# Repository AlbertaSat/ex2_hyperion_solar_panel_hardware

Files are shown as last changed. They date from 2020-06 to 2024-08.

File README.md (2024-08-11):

# Hyperion_Solar_Panels

This repository contains documentation describing the design of modular, open-source, deployable panels for CubeSats. 

The directory of the repository contains:

	- Documentation
		- All documents describing the designs, methods to adapt the design, and methods to analyze the effectiveness of the design
  
	- PCB Design files
		- Altium Designer project files for AlbertaSat's open-source Solar Panel design, dubbed "Hyperion"
  
	- CAD Files
		- 3D CAD files of the panel designs and components used on the panels

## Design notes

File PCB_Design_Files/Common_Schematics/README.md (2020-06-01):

These are schematics used by all Hyperion Solar Panels.

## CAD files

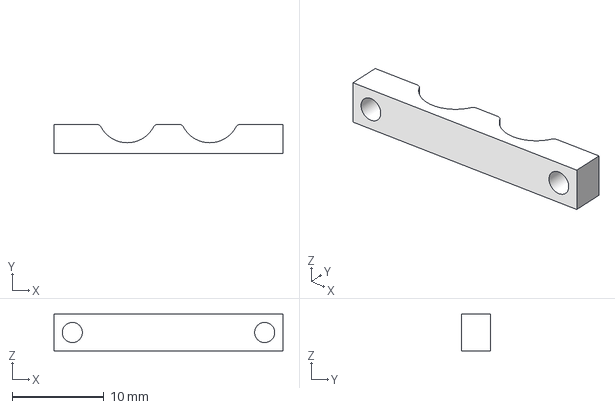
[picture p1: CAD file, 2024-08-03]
CAD_Files/20210528_DFGM_Saddle.step
25.0 x 3.18 x 4.00 mm

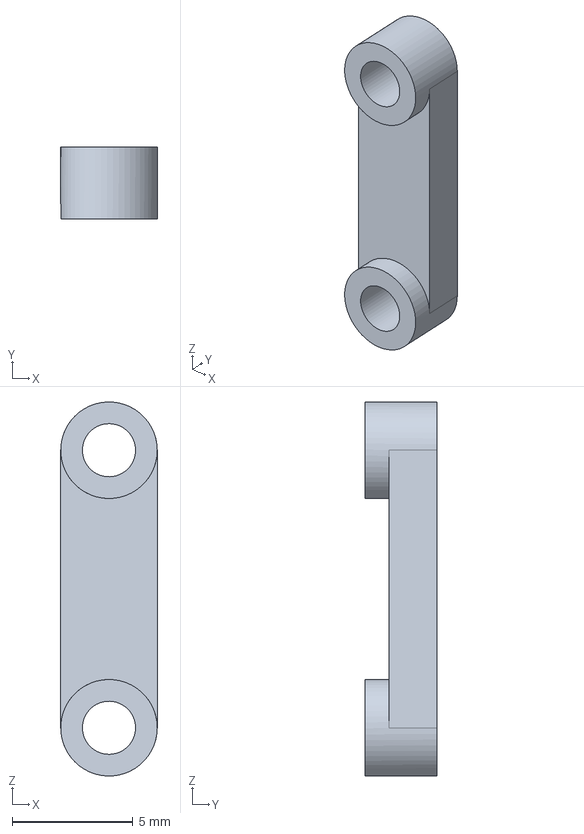
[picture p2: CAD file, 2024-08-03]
CAD_Files/20210528_Deployable_Switch_Depressor_Raised.step
4.00 x 3.00 x 15.5 mm

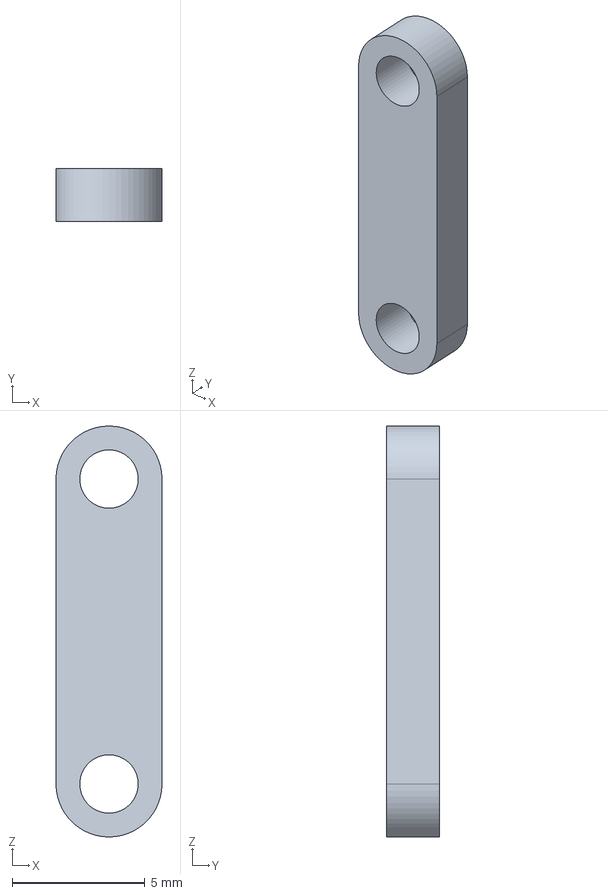
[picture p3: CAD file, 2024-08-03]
CAD_Files/20210528_Deployable_Switch_Depressor.step
4.00 x 2.00 x 15.5 mm

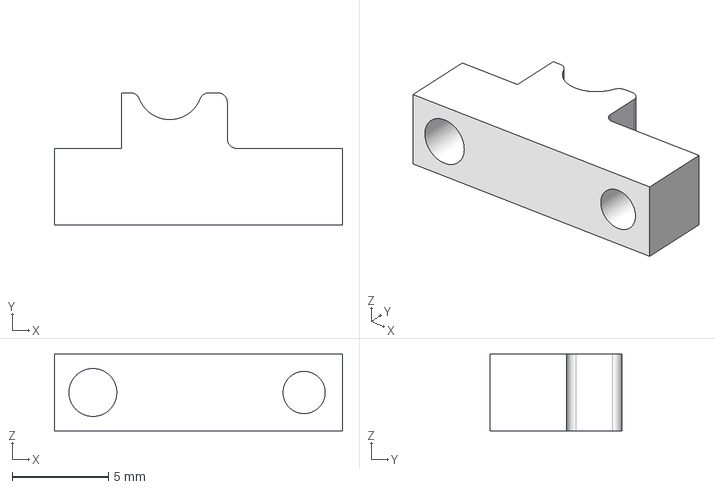
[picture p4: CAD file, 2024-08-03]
CAD_Files/20210823_Antenna_Saddle_2U.step
15.0 x 6.90 x 4.00 mm

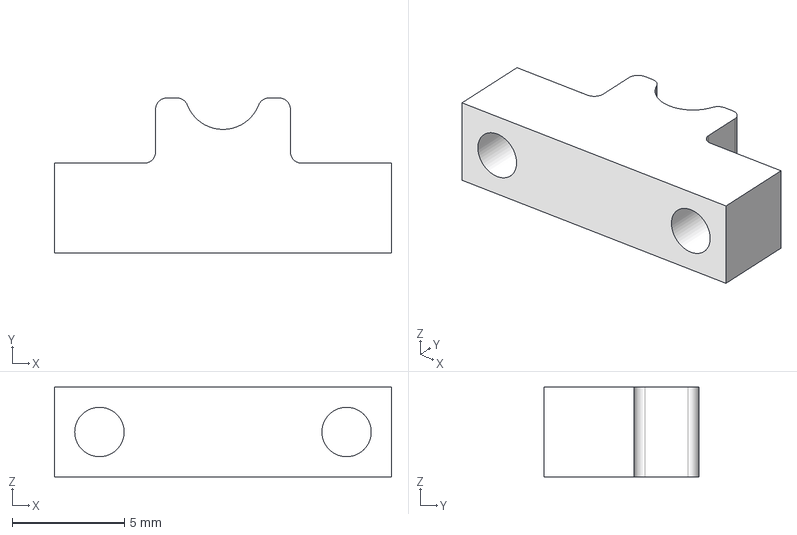
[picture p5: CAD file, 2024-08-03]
CAD_Files/20210528_Antenna_Saddle.step
15.0 x 6.90 x 4.00 mm

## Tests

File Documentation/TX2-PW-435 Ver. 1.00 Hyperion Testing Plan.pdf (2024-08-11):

# AlbertaSat

# Ex-Alta 2

# Hyperion Testing Plan

# Version 1.00

# July 20, 2020

University of Alberta

Institute for Space Science Exploration and Technology

Hyperion Testing Plan | TX2-PW-406 Ver. 1.00
AlbertaSat, University of Alberta | July 20, 2020

# Document Authentication

Prepared by

Name | Position | Signature | Date
Dineth Jayasekera | Power Team Member | | July 20, 2020
Nash Gould | Power Lead | | July 20, 2020

Reviewed by

Name | Position | Signature | Date
Nicholas J. Sorensen | Systems Engineer/Power Lead | | July 20, 2020
T. Haluza-Delay | Systems Engineer | | July 20, 2020

The undersigned acknowledge that they have reviewed the Hyperion Testing Plan, and they authorize the objectives, rules, and organization of the project as described in this document. Any changes to this Hyperion Testing plan will be coordinated with and approved by the undersigned or their designated representatives.

Approved by

Name | Position | Signature | Date
Nicholas J. Sorensen | Systems Engineer/Power Lead | | July 20, 2020
T. Haluza-Delay | Systems Engineer | | July 20, 2020

# Record of Document Changes

Version | Effective Date | Author(s) | Section(s) Changed | Description of Change(s)
0.10 | N/A | Dineth Jayasekera, Shirley Wang | All | Creation of Document
0.11 | July 10, 2020 | Nicholas J. Sorensen | All | Corrections in all sections, as well as formatting.
1.00 | July 20, 2020 | | All | PCB Component Testing Finalized

# Executive Summary

This document outlines the testing to be done on the various components of the Hyperion solar panel system being flown on the Ex-Alta 2 cubesat, and is largely based on standard ECSS-E-ST-20-08C [R1]. The following sections outline the equipment needed for tests, the safety measures taken before, during, and after testing, the procedures for each test, and the pass-fail criteria for each test.
The XTJ Prime solar cell assembly (SCA) will be tested to ensure that the cells meet the specifications outlined in the datasheet provided by Spectrolab, in addition to any other specifications given to AlbertaSat at the time of purchase. Testing done on the SCAs will include electrical performance testing, visual inspections, and verification of the pre-installed bypass diode on the XTJ-Prime solar cells. The solar panels, or the photo-voltaic assembly (PVA), will go through various qualification tests to ensure that they are capable of providing power required for the Ex-Alta 2 mission, in addition to withstanding a LEO environment. Testing on the PVA will include qualification testing and acceptance testing. This ensures that the Hyperion PVA is capable of performing as designed and will be ready for flight aboard Ex-Alta 2. Tests will ensure that the solar panels are capable of withstanding a range of temperatures and humidities, in addition to a reasonable amount of electro-static discharge (ESD). Testing on the Hyperion PVA will be conducted during and after assembly to ensure that the solar panels are built to mission specifications.

# Table of Contents

Document Authentication | 1
Record of Document Changes | 2
Executive Summary | 3
List of Figures | 8
Reference Documents | 9
Overview | 12
Safety and Handling Procedures | 13
Environmental Conditions | 13
Test tolerances and accuracies | 13
Parts, materials, and process parameters | 13
Toxicity | 13
Flammability | 14
Corrosion | 14
Magnetism | 15
Critical materials | 15
Solar cell assembly and component level testing | 16
Visual inspection | 16
Visual inspection for defects in the solar cell | 16
Visual inspection for defects In the coverglass | 17
Visual inspection for defects In the rear contacts | 18
Visual inspection for defects in the interconnectors | 18
Pass-fail criteria | 18
Dimensions and mass inspection | 18
Inspection of dimensions | 18
Mass compliance | 19
Electrical performance measurement | 20
PCB component testing | 22
Pre-PCB assembly testing | 22
Mechanical board dimension check | 22
Electrical continuity check | 22
Grounding resistance check | 23
Post-PCB assembly testing | 23
Electrical continuity check | 23

Magnetorquer testing | 24
Power Consumption | 24
Voltage Applications | 24
Photodiode testing | 25
Temperature sensor testing | 25
Voltage and current sensor testing | 26
Deployment mechanism testing | 29
Burnwire resistor cycling | 29
Burnwire thread burning | 29
Photovoltaic assembly testing | 30
SCA application testing | 30
Mass measurement | 30
Dry insulation test | 31
Adherence to PCB | 32
Visual Inspection | 33
Electrical continuity check | 34
Grounding resistance check | 36
Blocking diode Test | 36
Qualification testing | 37
Acceptance testing | 38
Definitions of tests | 39
Full visual inspection | 39
Electrical health check | 39
Electrical performance measurement | 39
Capacitance test | 39
Humidity Test | 42
Vacuum Thermal Cycling Test | 44
Acronyms and Abbreviations | 45
Appendix A: Hyperion Testing Parameters | 46
Appendix B: Equipment Calibration | 48
Vernier Caliper Padding | 48
Appendix C: Unnecessary Tests | 50
Electron Irradiation | 50
Photon Irradiation and Temperature Annealing | 51
Ultraviolet Exposure Test (UV) | 52
Thermo-Optical Data | 53
Coating Adherence | 55

Contact Thickness and Uniformity | 55
Temperature Coefficients Check | 56
Outgassing | 56
Surface Conductivity Test | 59
Reflectance Test | 59
Hemispherical Reflectance | 60
Coverglass gain-loss | 60
Active Passive Interface Test | 60
Spectral Response | 60
ESD Test | 60

# List of Figures

Table 1.1 - Temperature test tolerances
Figure 1.1 - WHMIS 2019 health hazard symbols
Figure 1.2 - WHMIS 2019 flammable/explosive hazard symbols Figure 1.3 - WHMIS 2019 corrosive hazard symbol
Figure 2.1 - Diagram of Cell Defects
Table 2.1 - Maximum Dimension of Each Defect
Figure 2.2 - Location of contacts
Figure 2.3 - Diagram of XTJ Prime Cell showing measurement points for cell thickness Figure 2.4 - I-V Measurement circuit schematic
Figure 2.5 - Electrical performance measurement set-up
Figure 2.6 - Characteristic I-V curve
Figure 3.1 - Voltage sense schematic
Figure 3.2 - Current sense schematic
Figure 3.3 - Burnwire resistor schematic
Figure 4.1 - Dry Insulation Test connections
Figure 4.2 - Attaching the 2 Kapton foils described in step 3 Figure 4.3 - Solar Cell Continuity Check Schematic
Figure 4.4 - Solar Panel Photodiode Sun Sensor Schematic
Figure 4.5 - Blocking Diode test schematic for the Port Solar Panel
Table 4.1 - The order of checks and tests to be done for each test
Table 4.2 - Shows the order in which checks should be run for acceptance testing. Figure 4.6 - Equivalent schematic of measurement circuit
Figure 4.7 - Physical Diagram of the Measurement Circuit
Figure 4.8 - a) A typical v-t characteristic (left)
and b) a realistic v-t characteristic due to parasitic inductance (right) Figure 4.9 - v-t characteristic with line of best fit
Figure 4.10 - A v-t characteristic with capacitance measurements
Fig 4.11 - PVA placed upright inside a Temperature - Humidity chamber

# Reference Documents

Ref. No | Document Name | Description
R01 | ECSS-E-ST-20-08C_REV-1-Photovoltaic Assemblies and Applications (https://drive.google.com/open?id=1e7iEEMibtRSNh4r5PsDM7qt9K71p06-v) | Standards document for PVA and SCA assembly.
R02 | XTJ Prime Solar Cell Datasheet (https://drive.google.com/file/d/0B97d2bqnH0zkVlVuVkE2MGp6ZE9UczJwQ3VCZWdjbzFfLW1r/view?usp=sharing) | XTJ Prime Solar Cell Datasheet.
R03 | 26.62 cm XTJ Prime Data Sheet (https://drive.google.com/open?id=183z8vA6ApDNlvgNMVB-VMi8t07TAn0pB)
R04 | Nimals Thesis - Nanosatellite Electrical Power System Development (https://drive.google.com/file/d/1hn5aqBO2z6VRZzP0JX6DqySkAxhxV4oR/view?usp=sharing)
R05 | Solar Panel GitHub Repository (https://github.com/AlbertaSat/Hyperion_Solar_Panels/)
R06 | ASTM E1462-12 Standard Test Methods for Insulation Integrity and Ground Path Continuity of Photovoltaic Modules | Used section 7.2 in page 3 for the Insulation Integrity, Insulation Resistance
R07 | Solar Cell Capacitance Determination Based on RLC Resonant Circuit | Used information from this to write the overview of a Capacitance Test in section 3.4.4
R08 | Solar Cell Capacitance Measurement Paper R. Blok (https://drive.google.com/file/d/14LIBwxDeGmqE0Z6AtOoJMlMoXcoapYHf/view?usp=sharing) | Research paper on Time domain capacitance measurement for Multi-Junction PVA and SCA
R09 | ASTM D1193-99: Standard Specification for Reagent Water | Standard Specification for Reagent Water
R10 | TX2-PW-406 Ver 1.00 Hyperion Solar Panels Interface Control Document (https://docs.google.com/document/d/1ZF8Y04XHxNmc1AYKCmSLeX3bC2qYf7z2ltytlE_TRUk/edit?usp=sharing)
R11 | CV-2289 Adhesive Datasheet (https://drive.google.com/file/d/1lksphBZLpFXucOKJV0rzpvgfndgTXVmK/view?usp=sharing)
R04 | Electrostatic Discharge Testing on Meteosat 3rd (https://drive.google.com/file/d/14aZHrpDwEIz-mOJ8zAYnhdjg1PYSGra5/view?usp=sharing)

| Generation Photovoltaic Assembly (https://drive.google.com/file/d/14aZHrpDwEIz-mOJ8zAYnhdjg1PYSGra5/view?usp=sharing)
R13 | ECSS-Q-ST-70-06C Particle and UV Radiation Testing for Space Materials (https://drive.google.com/file/d/1VEsK8YueqFWnclV3nJhuqDO76dNOLiTn/view?usp=sharing) | ECSS document detailing UV radiation process
R14 | Solar Cell Radiation Handbook NASA (https://drive.google.com/file/d/1d_dKATuudc_2SWbYDcYr1uuwGrd_dQxY/view?usp=sharing)
R15 | Thermal Annealing of Radiation Damage in Solar Cells - Goddard Space Flight Center (https://drive.google.com/file/d/1DUtyBk_aHcihWG-Gnc6Qpf9xUuCX0HYQ/view?usp=sharing)
R16 | Test Techniques for Voltage and Humidity-Induced Degradation of Thin Film Photovoltaic Modules -Jet Propulsion Laboratory (https://drive.google.com/file/d/1DUtyBk_aHcihWG-Gnc6Qpf9xUuCX0HYQ/view?usp=sharing)
R17 | ISO-23038: Space systems — Space solar cells — Electron and proton irradiation test methods | Electron and proton irradiation test methods for photovoltaic cells
R18 | ISO 9211-4: Optics and photonics - Optical coatings - Part 4 Specific test methods
R19 | Accelerated UV Testing and Characterization of PV Modules with UV - cut and UV - pass EVA Encapsulants by Kshitiz Dolia (https://drive.google.com/file/d/1_bruaEFhISPj-MZBzRWybPWMlPLE752r/view?usp=sharing)
R20 | Electrical Isolation Design and Electrochemical Corrosion in Thin Film Photovoltaic Modules -Jet Propulsion Laboratory (https://drive.google.com/file/d/1xiNpXD-C_T9-3XhJVlm7x-XevL9Cx3Tr/view?usp=sharing)
R21 | Solar Radiation - Qiang Fu, (https://drive.google.com/file/d/1PRftebfSfHzLcuw8mMy50l51dxaLHDcr/view?usp=sharing) Page 1859 | Got values of solar intensity of UV light from this (for the UV test)
R22 | ASTM E948-16: Standard Test Method for Electrical Performance of Photovoltaic Cells Using Reference Cells Under Simulated Sunlight

R23 | ASTM E2236 - Standard Test Methods for Measurement of Electrical Performance and Spectral Response of Non Concentrator Multijunction Photovoltaic Cells and Modules
R24 | ASTM: E1802 − 12 - Standard Test Methods for Wet Insulation Integrity Testing of Photovoltaic Modules
R25 | Solar Cell Performance Measurement F.C Treble (https://drive.google.com/file/d/1NRIMmkoJcFSVu136WJdcnpuidz_4xrMm/view?usp=sharing) | Research paper on basic methods of how solar cells can be measured (from 1965 so is a bit dated)
R26 | <Removed>
R27 | ecss-q-st-70-02c Thermal Vacuum Outgassing Test (https://drive.google.com/file/d/1gFmYXbCWnB96BwieAUklcGbwXe3g5Ucf/view?usp=sharing) | ECSS document detailing how the Thermal Vacuum Outgassing test should be carried out

# Overview

This document outlines the testing to be done on the various components of the Hyperion solar panel system being flown on the Ex-Alta 2 cubesat, and is largely based on standard ECSS-E-ST-20-08C [R01]. The following sections outline the equipment needed for tests, the safety measures taken before, during, and after testing, the procedures for each test, and the pass-fail criteria for each test.
The XTJ Prime solar cell assembly (SCA) will be tested to ensure that the cells meet the specifications outlined in the datasheet provided by Spectrolab, in addition to any other specifications given to AlbertaSat at the time of purchase. Testing done on the SCAs will include electrical performance testing, visual inspections, and verification of the pre-installed bypass diode on the XTJ-Prime solar cells. The solar panels, or the photo-voltaic assembly (PVA), will go through various qualification tests to ensure that they are capable of providing power required for the Ex-Alta 2 mission, in addition to withstanding a LEO environment. Testing on the PVA will include qualification testing and acceptance testing. This ensures that the Hyperion PVA is capable of performing as designed and will be ready for flight aboard Ex-Alta 2. Tests will ensure that the solar panels are capable of withstanding a range of temperatures and humidities, in addition to a reasonable amount of electro-static discharge (ESD). Testing on the Hyperion PVA will be conducted during and after assembly to ensure that the solar panels are built to mission specifications.
The tests in this document should be performed in the following order:
1. SCA Acceptance Tests (Chapter 2)
2. PCB Component Tests (Chapter 3)
3. PVA Tests (Chapter 4)
a. In-Process PVA Tests
b. Qualification PVA Tests
c. Acceptance PVA Tests
The solar panels will have been qualified engineering models once all SCA acceptance tests have been performed on the solar cells, the PCB component tests have been performed on each panel, and the PVA tests have been performed on each panel.

# 1. Safety and Handling Procedures

The following procedures are to be followed in all testing and handling of Hyperion components to ensure operational safety.

## 1.1. Environmental Conditions

Atmospheric conditions during inspection, testing, and storage, unless specified otherwise, must be as follows:
1. Pressure: 101.325 ± 3.3 kPa
2. Temperature: 23 ± 5 C
3. Average relative humidity: 40 - 60%
In addition, the room cleanliness level should be airborne particle count: Class 8 ISO 14644-1. Any deviation from the above conditions should be recorded [R1].

## 1.2. Test tolerances and accuracies

In the following tests, the accuracy of the instruments and equipment used to measure and control test parameters should be an order of magnitude higher than the tolerance on the variable to be measured, with the exception of mass and temperature measurements. The accuracy of mass measurements should be better than ±1% of the mass or 0.01g, whichever is more accurate. The test temperature tolerances for any thermal testing are given in table 1.1 below. All equipment and instruments used should be calibrated properly before testing. Instruments should be recalibrated daily during testing [R01].
Vernier Calipers should always be padded before use in measurement. Refer to 5.3 Vernier Caliper Padding
Temperature Range (°C) | Tolerance (°C)
-40 to -30 | -10/0
-30 to +60 | -5/+5
+60 to +70 | 0/+10

Table 1.1 - Temperature test tolerances. This shows the maximum acceptable deviation in temperature during a thermal test [1] i.e. the temperature can vary from -50 to -40 when conducting thermal cycling at -40 ℃.

## 1.3. Parts, materials, and process parameters

### 1.3.1. Toxicity

1. Identify, and create a log of materials used during the design/construction process that can cause injury. Toxic materials can be identified by checking the case/packaging for the below Hazard symbols

Figure 1.1 - WHMIS 2019 health hazard symbols

2. Not all companies use these symbols so also look for health/toxicity warnings on labels
3. Use gloves and other appropriate protective apparel when handling toxic materials (ie: face masks)
4. Describe precautions to be taken when handling these materials.

### 1.3.2. Flammability

1. Identify, and create a log of flammable materials used in the design/construction process. Toxic materials can be identified by checking the case/packaging for the below Hazard symbols

Figure 1.2 - WHMIS 2019 flammable/explosive hazard symbols

2. Not all companies use these symbols so look for warnings about flammability/ combustibility on labels.
3. Ensure that flammable materials are stored safely, and are not used in situations where they may combust (ie: used near possible ignition sources and oxygen)

### 1.3.3. Corrosion

1. Consider the effects of corrosion on the photovoltaic cells during both storage, and during operation. This can be done by estimating the corrosion rate of the PVA system for both the duration in storage and in operations and estimating the level to which the PVA might corrode in that duration.
2. Take the atmosphere conditions 101.325 kPa at 27 C for 5 years.

Figure 1.3 - WHMIS 2019 corrosive hazard symbol

3. Look for electrolytic corrosion erosion near metal-metal interfaces with current flow, and contact with an electrolyte. This is most common near batteries or similar devices.

### 1.3.4. Magnetism

1. Use only non-magnetic materials. Any permanent magnets used should be recorded. Check for closed loops in the PCB, 90° angle traces, and minimum high speed trace lengths by reviewing all board designs for Hyperion. The Hyperion does not have high speed traces however this is something to keep on mind.

### 1.3.5. Critical materials

1. All silver cladding used must be annealed, and must be 99.9% pure silver
2. There can be no pure Tin, Cadmium, or Zinc in the finished space-qualified solar panels.
a. Pure Tin can be a tin alloy with less than three atomic percent of the alloying metal.
b. Pure Cadmium and Zinc refer to when they are used non-mixed or unalloyed.
3. Solar panels containing Beryllium Oxide should be clearly identified
All of these requirements are from [R01].

# 2. Solar cell assembly and component level testing

Testing done on the SCA will be to verify that the XTJ Prime solar cells will perform to specification given in the datasheet in [R02]. All testing in this section is to be done at atmospheric pressure and room temperature. Testing on XTJ Prime solar cells will involve visual inspections, power generation characterisation, and bypass diode characterisation.

## 2.1. Visual inspection

All SCAs received from Spectrolab must be visually inspected to ensure that they are free of physical defects and that they are within the dimensions given within the datasheet. The following tests analyze the various parts of the SCA and ensure that each is capable of performing properly and withstanding a LEO environment [R01].

Materials:
1. Magnifying glass
2. Padded Digital vernier calipers - Refer to Vernier Caliper Padding

### 2.1.1. Visual inspection for defects in the solar cell

1. Search for edge chips, corner chips, surface nicks and record any found.
a. Edge chips: Defects along the edges of the cell
b. Corner Chips Defects near the corners of the cell
c. Surface nicks: Defects or blemishes on the surface of the cell
2. Estimate the length, and area of each defect using calipers and your judgement. The maximum length of each defect is shown below. Solar cells which fail this criteria will be rejected.

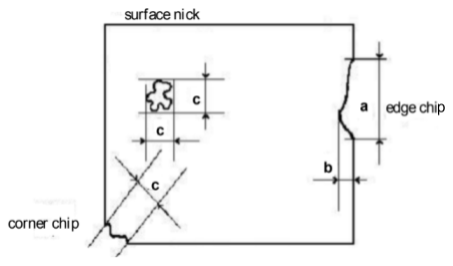
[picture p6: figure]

Figure 2.1 - Diagram of Cell Defects [1]

a | b | c
12 | 1.1 | 5

Table 2.1 - Maximum Dimension of Each Defect (mm) [R01]

3. The sum of all the areas of the defects found in step 2 must not exceed 1.33 cm

2
4. Focus on defects in the contact weld area as these could weaken interconnections between cells. Use judgement to decide whether the defects will cause any problems.
5. Check for fingerprints. Clean any found using Isopropyl alcohol and cleanroom wipes. Clean by wiping in one direction, the perpendicular direction and repeating.

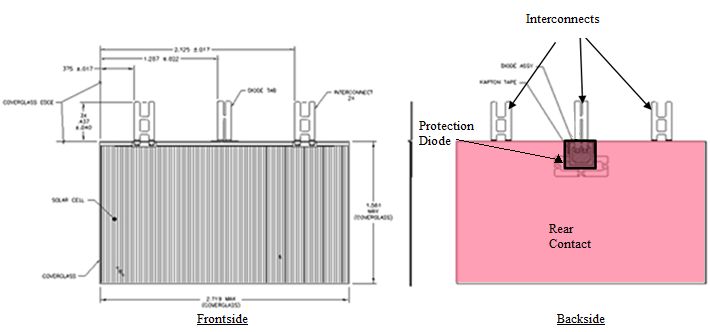
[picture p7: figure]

Figure 2.2 - Location of contacts

### 2.1.2. Visual inspection for defects In the coverglass

1. Inspect the SCA to ensure that the coverglass covers 100% of the bare solar cell.
2. Small surface defects less than 5mm in length on the coverglass can be ignored if the coverglass completely covers the solar cell.
3. Coverglasses with dirty and contaminated surfaces cannot be used. Clean using the isopropyl alcohol and cleanroom wipes. Carefully wipe in one direction, then wipe perpendicularly. Repeat.
4. Check for areas where the anti-reflective coating is missing/ scraped off. Estimate the area of any such regions. The sum of all such regions cannot exceed 0.8 cm

2
5. The coverglass should not contain any bubbles larger than 0.02mm

2
. Measure areas using
digital vernier calipers.
6. A coverglass cannot have
a. Cracks with a visible separation

b. More than 3 cracks
c. Meeting cracks with non-meeting ends separated by more than 2 mm
7. There should be no discolouration or delamination of the adhesive except in the area opposite the rear welds (where the connecting cells rear welds would attach)
8. Voids in the adhesive must be less than 0.6 mm in depth
9. The total estimated area of bubbles should not exceed 0.5 mm

2
- bubbles smaller than 0.02 mm

2
, and bubbles less than 2 mm away from the interconnector edges can be ignored for this test.

### 2.1.3. Visual inspection for defects In the rear contacts

1. Any SCAs with the following defects should not be used
a. Any drops and spatter are smaller than 0.1 mm in diameter and 0.05 mm in height.
b. Edge delaminations should not exceed 0.75 mm.
c. Defects should not exceed 5.3 mm

2

### 2.1.4. Visual inspection for defects in the interconnectors

There can be no breaking, tearing, or deformation of the interconnectors.

Pass-fail criteria
SCAs which do not meet the above requirements should not be used in the final PVA. These cells can be used for testing if the defect does not change the property being tested for.

## 2.2. Dimensions and mass inspection

### 2.2.1. Inspection of dimensions

This checks that the SCAs meet the dimensions given in the XTJ Prime documentation [R02].

Materials:
- Measuring tape
- Padded Digital vernier calipers/micrometer
- Mass scale
- Cleanroom wipes
- Isopropyl alcohol (99% or higher)

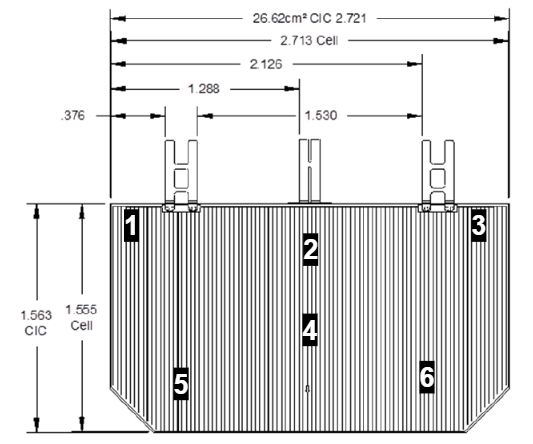
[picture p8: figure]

Figure 2.3 - Diagram of XTJ Prime Cell showing measurement points for cell thickness [R03]

Procedure:
1. Use the measuring tape to measure the length of each side of the SCA, and note down the dimensions of each SCA.
2. Measure and note down the thickness of the SCA at the numbered points shown in Figure 2.3 using calipers. Calculate the average thickness.
3. Check if the average thickness is between 80-225 µm. Note any cells which fall outside of this range.
4. Compare measured dimensions with the circuit diagrams, and footprints to ensure that all SCAs fit within the outlines of the PCB Board.

### 2.2.2. Mass compliance

Weigh each solar cell on a mass balance that meets the minimum tolerance stated in Section 1.2. Divide the mass of each Solar cell by its total area (Mass / 26 cm^2) and check if the obtained value is between 50-84 mg/cm^2 [R02]. Any solar cells outside of this range do not meet Mass Compliance.

## 2.3. Electrical performance measurement

This test measures the full IV characteristic curve of the XTJ Prime SCAs. Isc, Voc and Pmax are found/calculated from the curve. The measured Isc, Voc, and Pmax of the SCA are compared with the expected values.

Follow the manufacturer’s guidelines when setting up and calibrating the Solar Simulator.

Materials:
- Calibrated continuous solar simulator (Probably G2V Optics)
- Dark box/room
- Decade box
- Arduino system for data logging with current and voltage sensors

Procedure
1. Ensure that the solar simulator has been calibrated to emit 1 S.C (solar constant) at AM0, there is no spectral mismatch, and that the testing area is lit uniformly using test in appendix A.
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

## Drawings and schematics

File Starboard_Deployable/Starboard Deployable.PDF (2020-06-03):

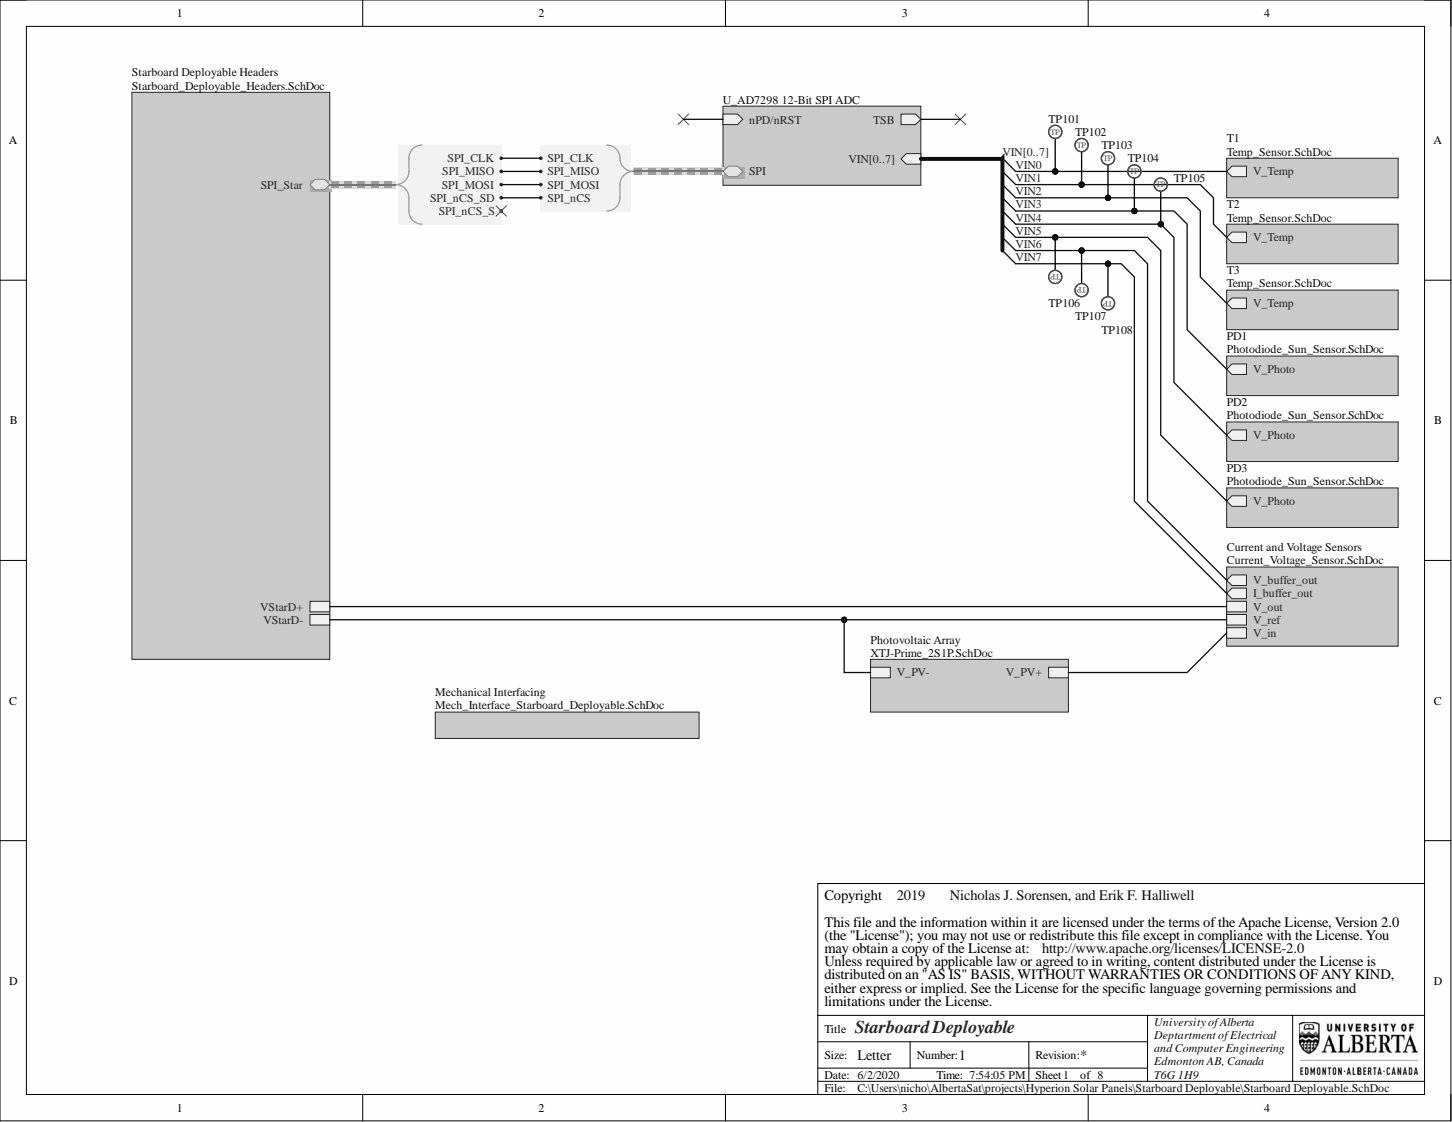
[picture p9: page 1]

(the "License"); you may not use or redistribute this file except in compliance with the License. You This file and the information within it are licensed under the terms of the Apache License, Version 2.0

may obtain a copy of the License at:
Unless required by applicable law or agreed to in writing, content distributed under the License is
distributed on an "AS IS" BASIS, WITHOUT WARRANTIES OR CONDITIONS OF ANY KIND, either express or implied. See the License for the specific language governing permissions and

http://www.apache.org/licenses/LICENSE-2.0

limitations under the License.
Starboard Deployable
Title

Letter
C:\Users\nicho\AlbertaSat\projects\Hyperion Solar Panels\Starboard Deployable\Starboard Deployable.SchDoc

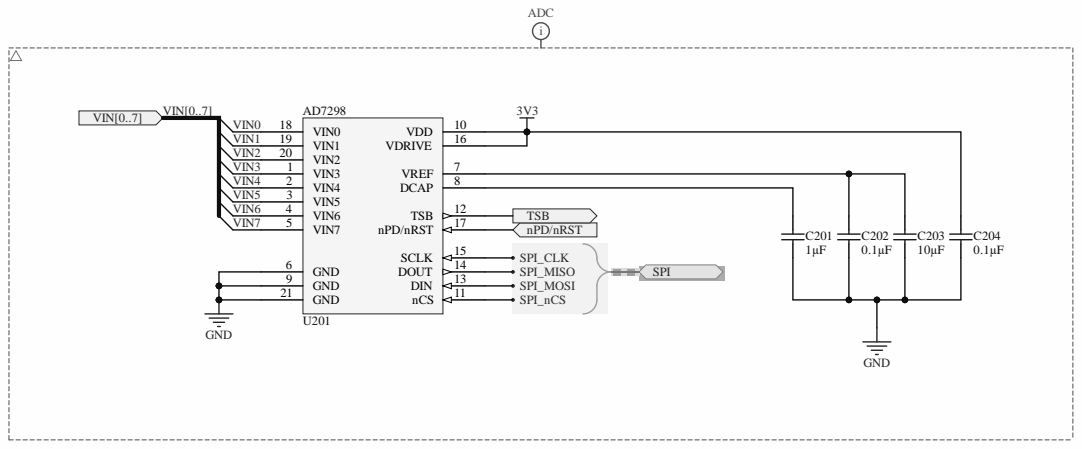
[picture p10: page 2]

1 2
1 7

9 | 1 3
2 1 | | 1 1

n within it are lic

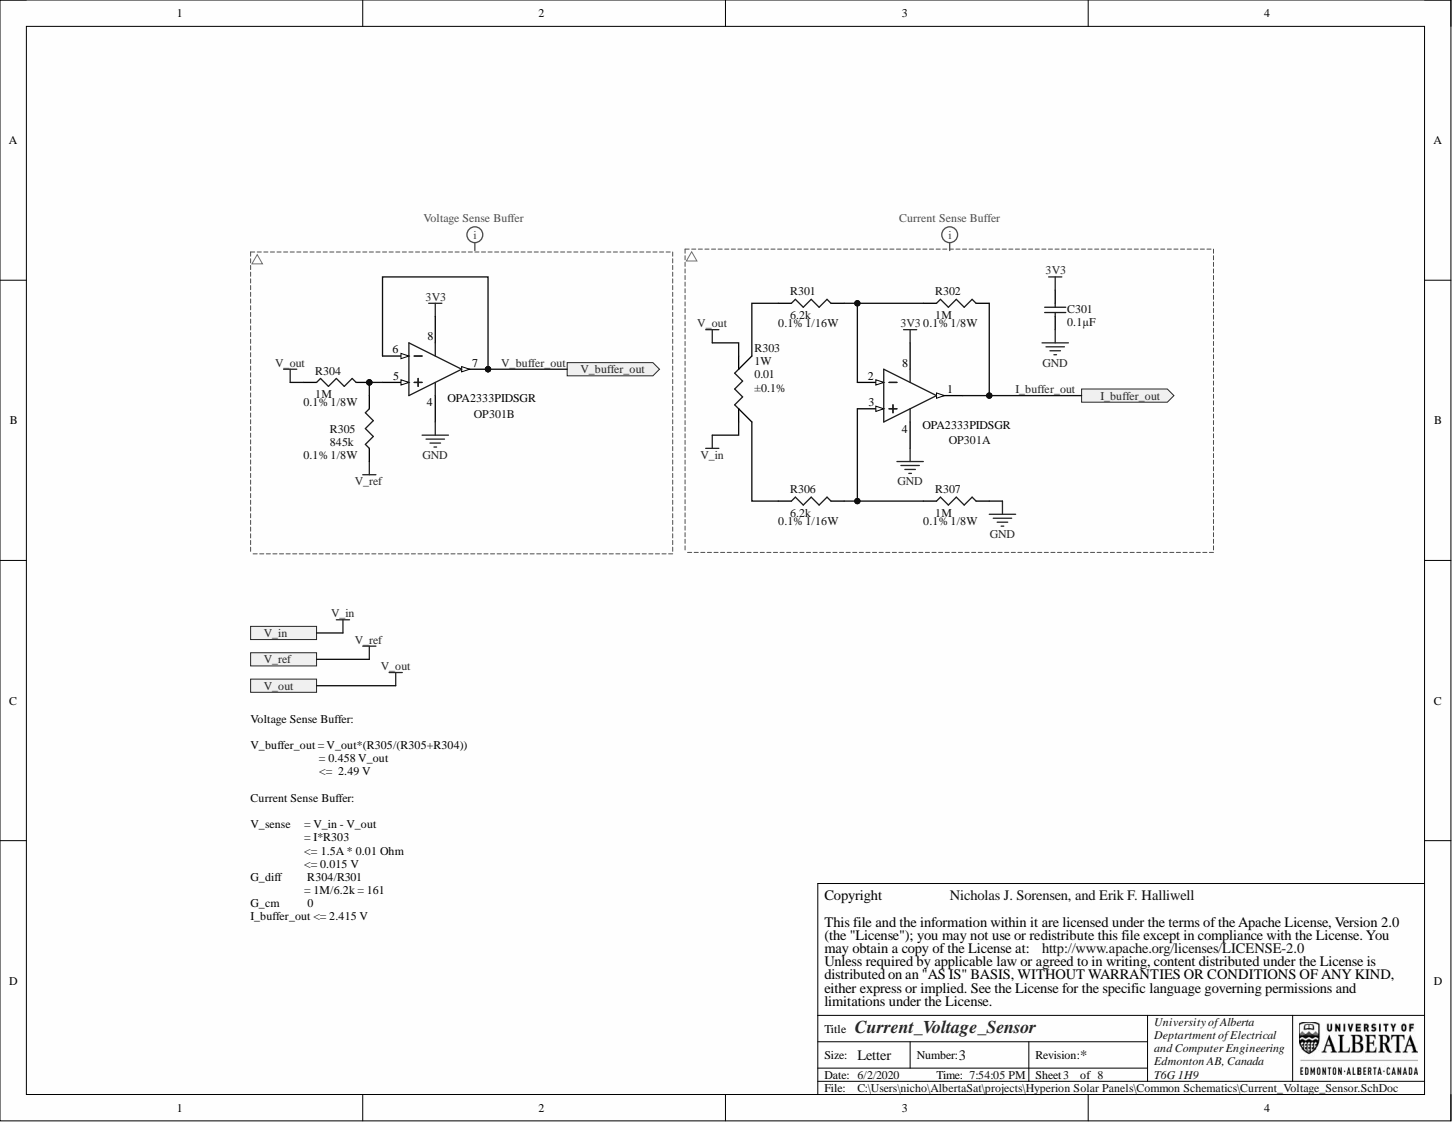
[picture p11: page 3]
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

http://www.apache.org/licenses/LICENSE-2.0

Letter
C:\Users\nicho\AlbertaSat\projects\Hyperion Solar Panels\Common Schematics\Current_Voltage_Sensor.SchDoc

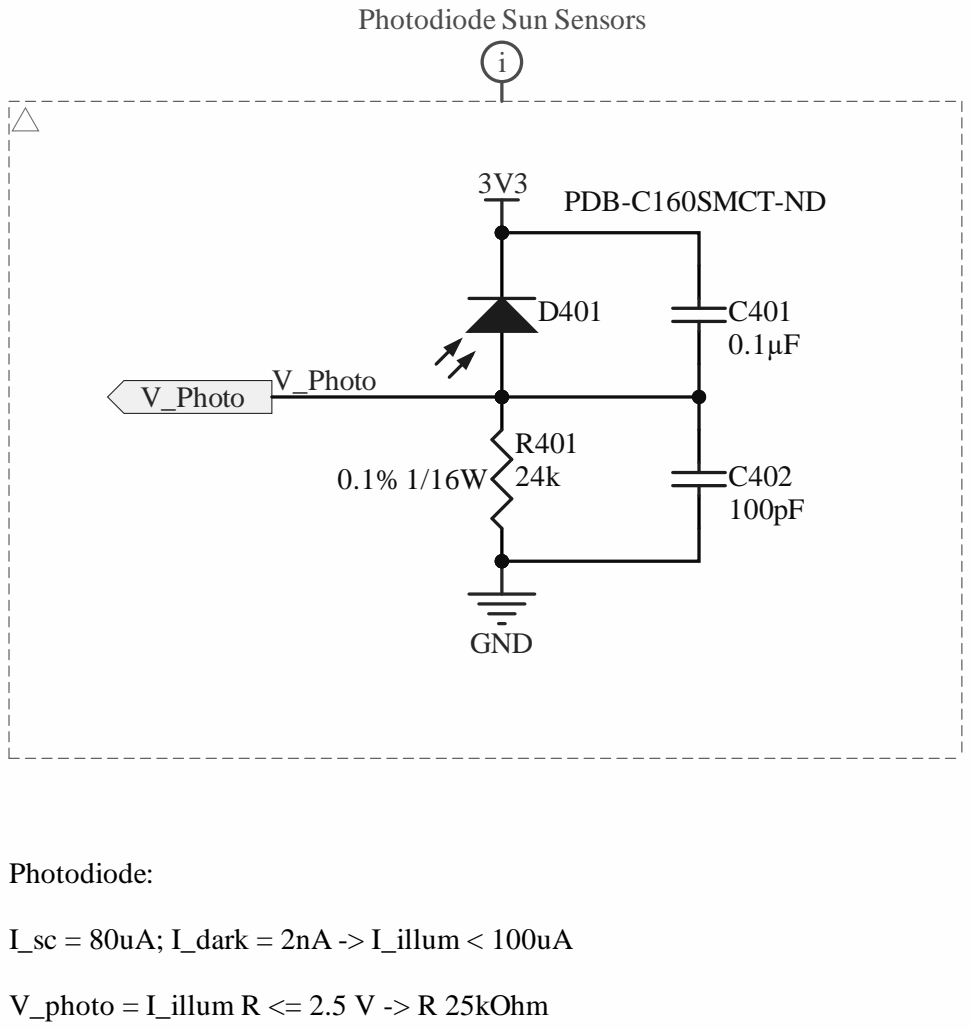
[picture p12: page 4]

n within it are lic

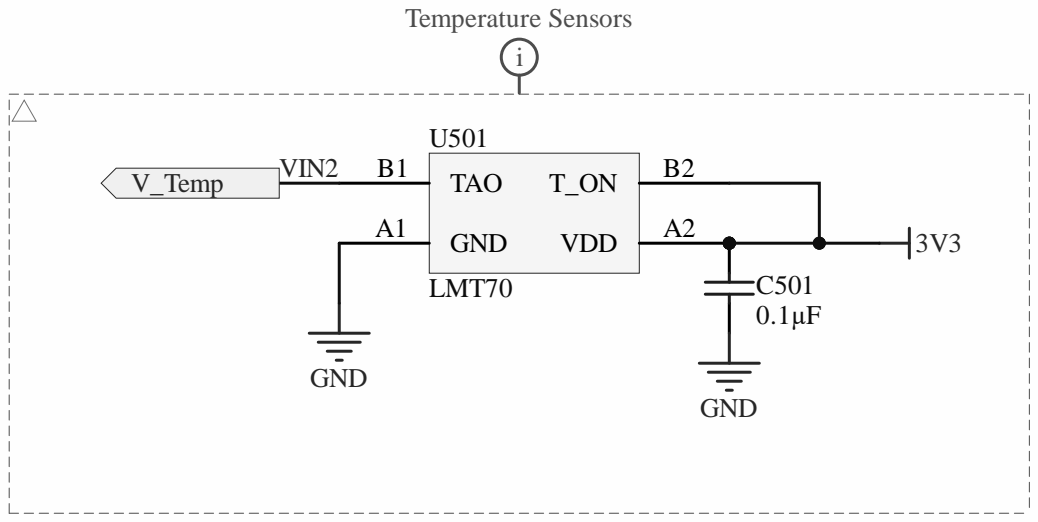
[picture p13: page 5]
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

http://www.apache.org/licenses/LICENSE-2.0

Letter
C:\Users\nicho\AlbertaSat\projects\Hyperion Solar Panels\Common Schematics\Temp_Sensor.SchDoc

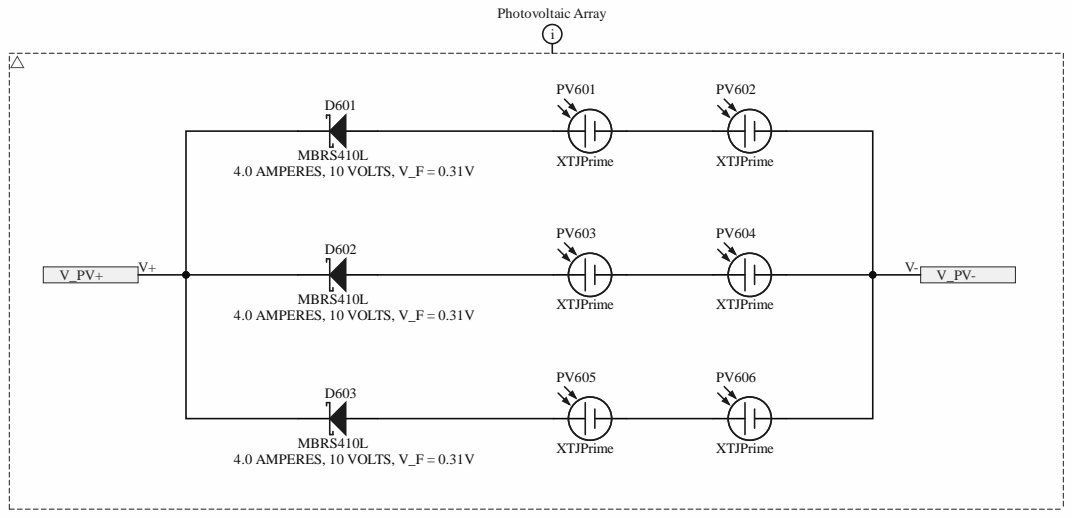
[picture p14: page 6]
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

http://www.apache.org/licenses/LICENSE-2.0

limitations under the License.
XTJ-Prime_2S2P
Title

Letter
C:\Users\nicho\AlbertaSat\projects\Hyperion Solar Panels\Common Schematics\XTJ-Prime_2S1P.SchDoc

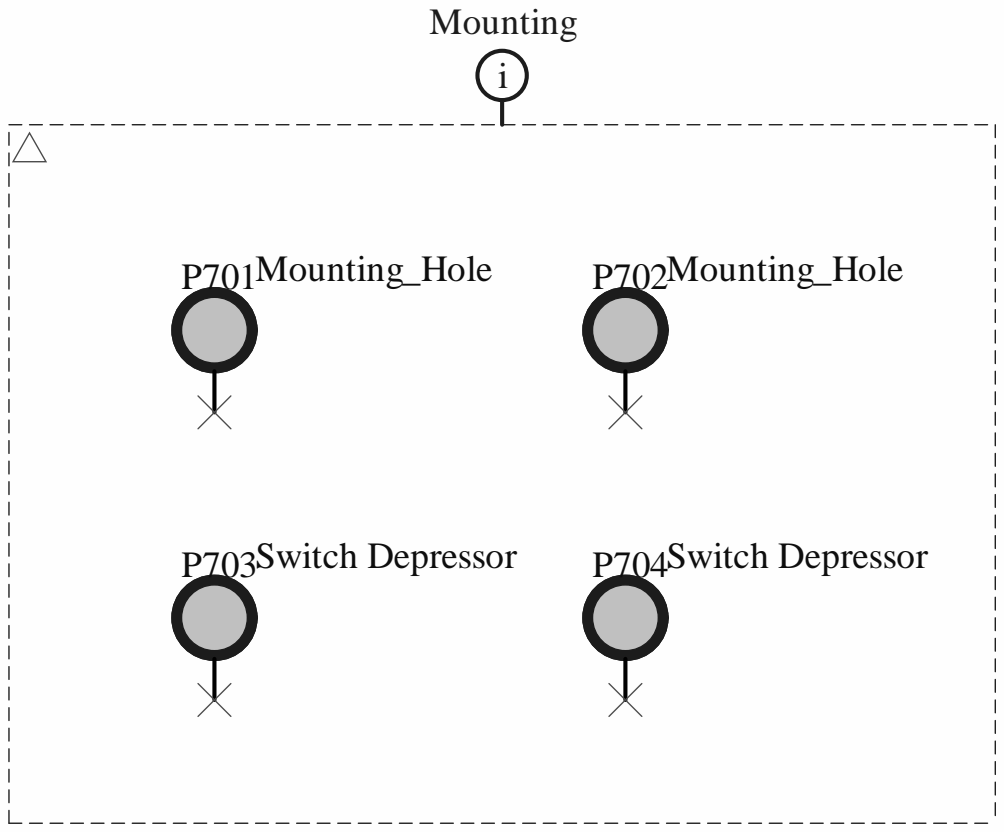
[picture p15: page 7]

n within it are lic

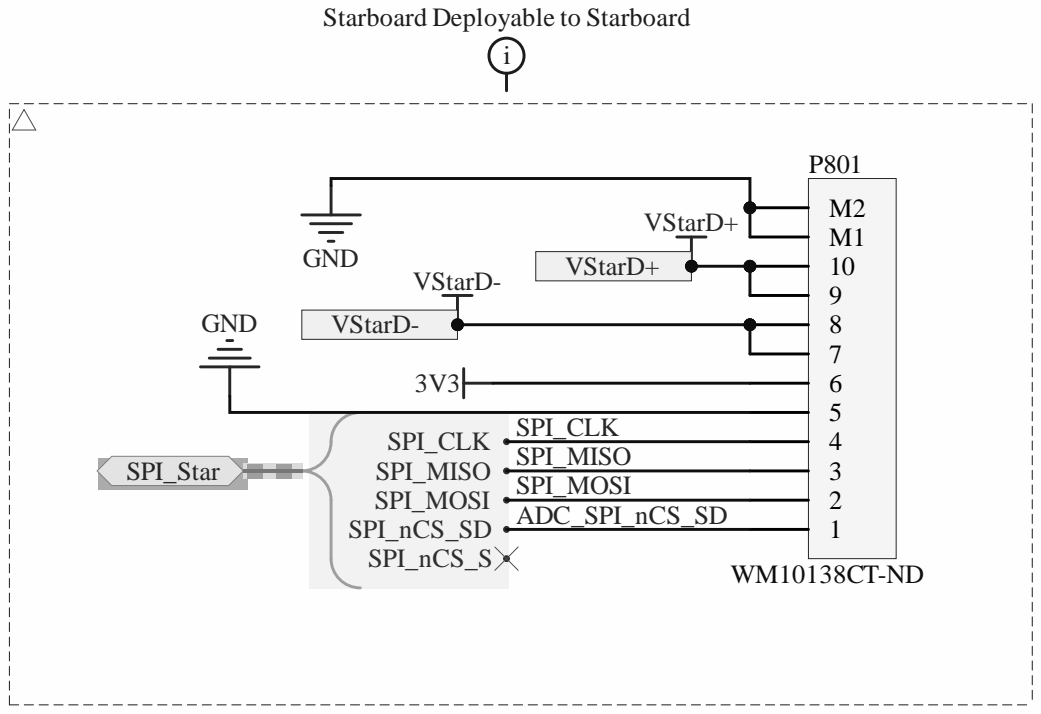
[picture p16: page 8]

Starboard Deployable to Starboard

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

http://www.apache.org/licenses/LICENSE-2.0

Letter
C:\Users\nicho\AlbertaSat\projects\Hyperion Solar Panels\Starboard Deployable\Starboard_Deployable_Headers.SchDoc

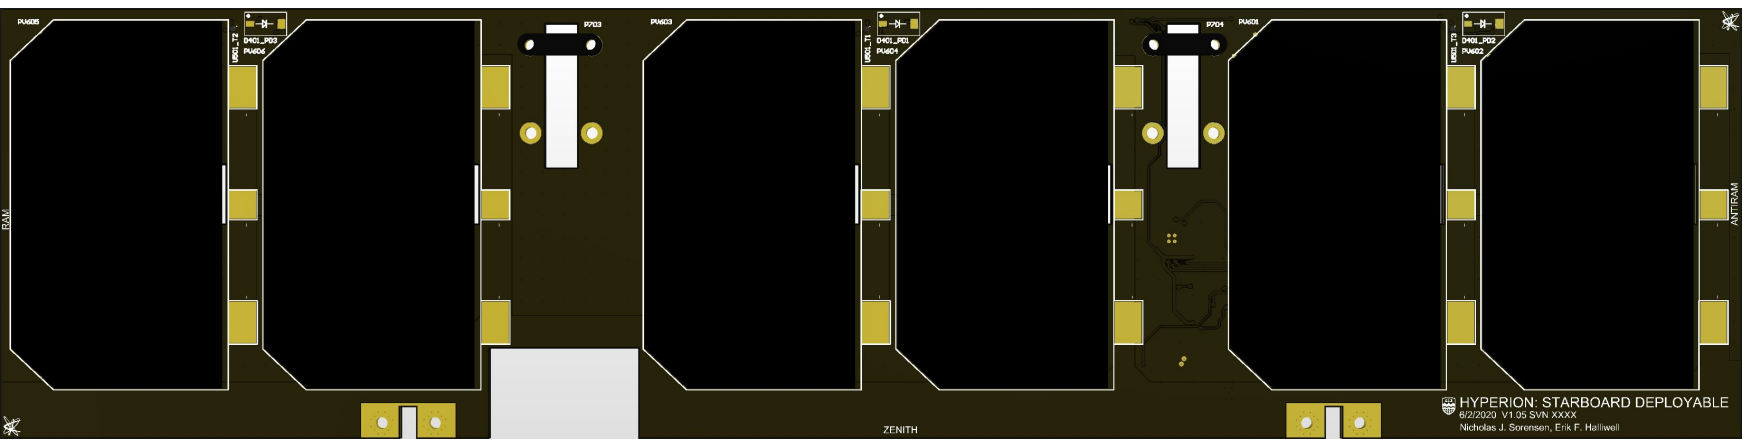
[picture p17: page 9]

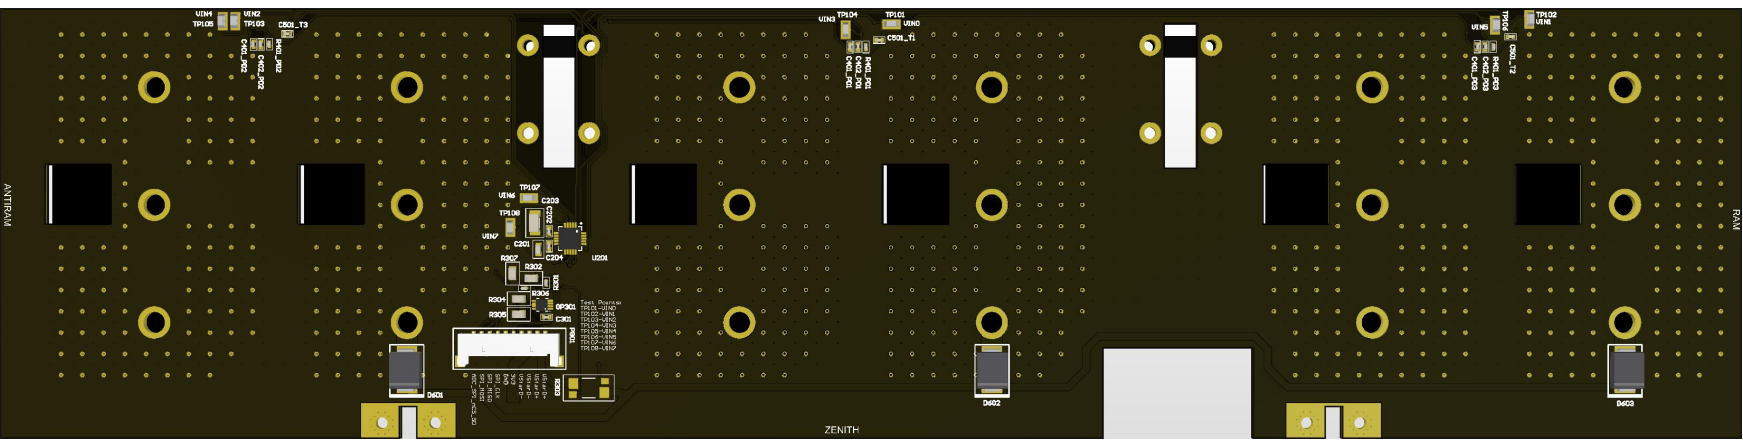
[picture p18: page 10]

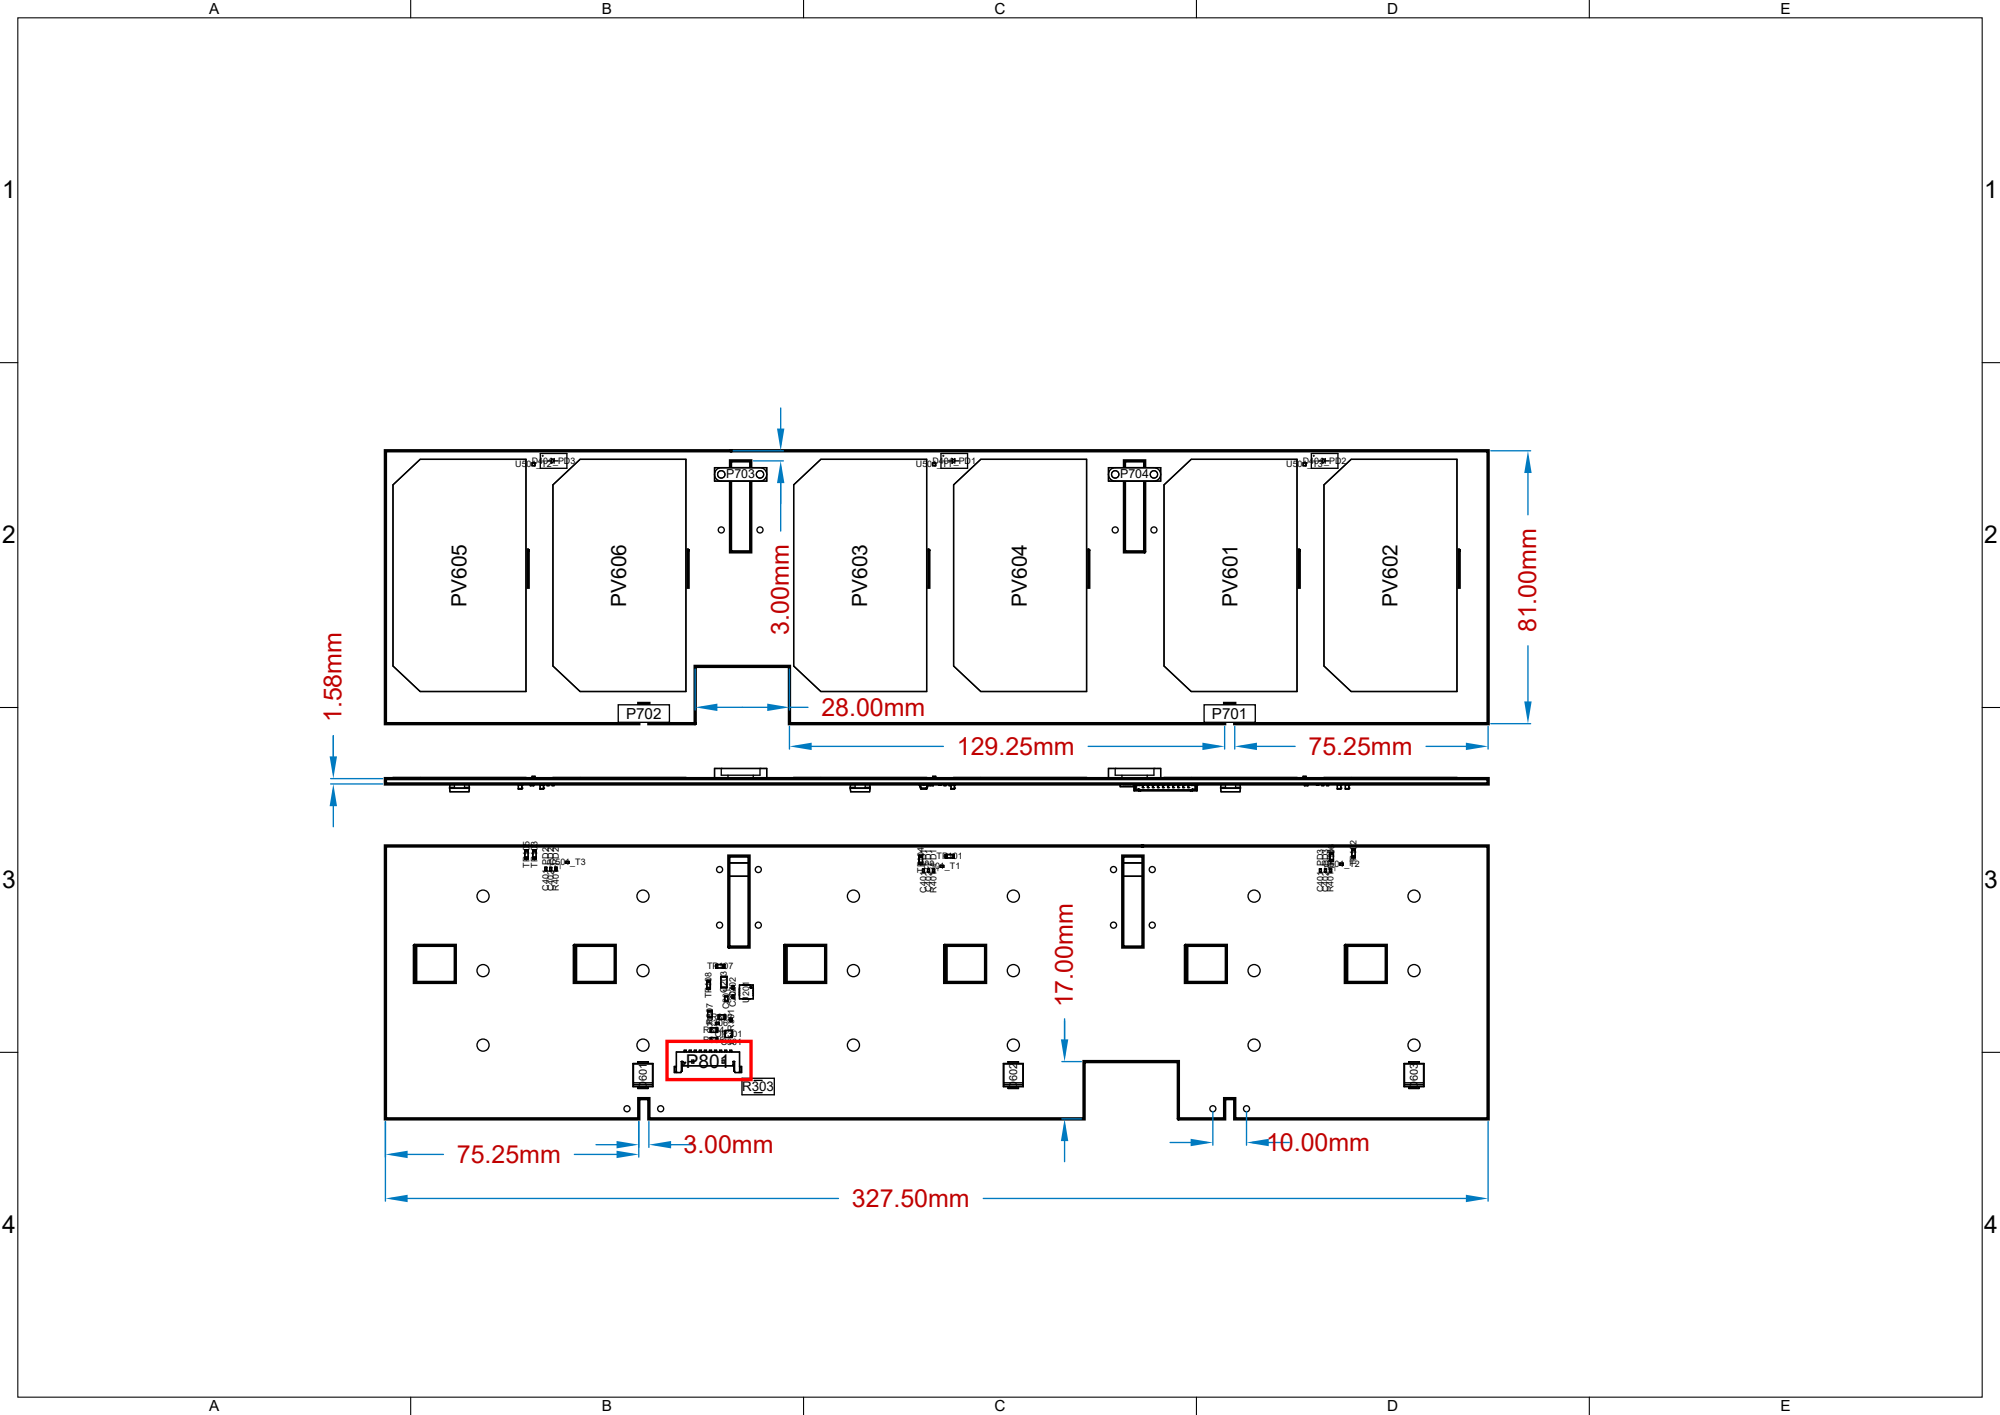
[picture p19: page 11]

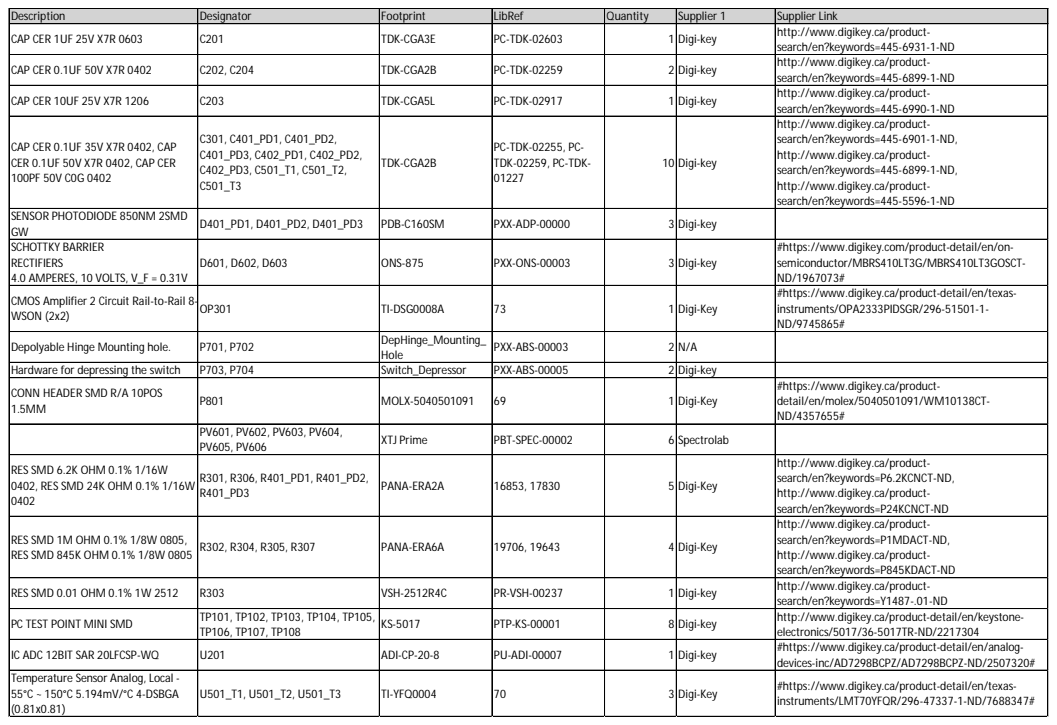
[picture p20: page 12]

Description | Designator | Footprint | LibRef | Quantity | Supplier 1 | Supplier Link
CAP CER 1UF 25V X7R 0603 | C201 | TDK-CGA3E | PC-TDK-02603 | 1 | Digi-key | http://www.digikey.ca/product-search/en?keywords=445-6931-1-ND

CAP CER 0.1UF 50V X7R 0402 | C202, C204 | TDK-CGA2B | PC-TDK-02259 | 2 Digi-key | | http://www.digikey.ca/product-search/en?keywords=445-6899-1-ND

CAP CER 10UF 25V X7R 1206 | C203 | TDK-CGA5L | PC-TDK-02917 | 1 | Digi-key | http://www.digikey.ca/product-search/en?keywords=445-6990-1-ND
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

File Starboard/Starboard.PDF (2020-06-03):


(the "License"); you may not use or redistribute this file except in compliance with the License. You This file and the information within it are licensed under the terms of the Apache License, Version 2.0

may obtain a copy of the License at:
Unless required by applicable law or agreed to in writing, content distributed under the License is
distributed on an "AS IS" BASIS, WITHOUT WARRANTIES OR CONDITIONS OF ANY KIND, either express or implied. See the License for the specific language governing permissions and

http://www.apache.org/licenses/LICENSE-2.0

limitations under the License.
Starboard
Title

Letter
C:\Users\nicho\AlbertaSat\projects\Hyperion Solar Panels\Starboard\Starboard.SchDoc


1 2
1 7

9 | 1 3
2 1 | | 1 1

n within it are lic

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

http://www.apache.org/licenses/LICENSE-2.0

limitations under the License.
Current_Voltage_Sensor

C:\Users\nicho\AlbertaSat\projects\Hyperion Solar Panels\Common Schematics\Current_Voltage_Sensor.SchDoc


n within it are lic

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

http://www.apache.org/licenses/LICENSE-2.0

limitations under the License.
Temp_Sensor

C:\Users\nicho\AlbertaSat\projects\Hyperion Solar Panels\Common Schematics\Temp_Sensor.SchDoc

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

http://www.apache.org/licenses/LICENSE-2.0

limitations under the License.
XTJ-Prime_2S2P

C:\Users\nicho\AlbertaSat\projects\Hyperion Solar Panels\Common Schematics\XTJ-Prime_2S1P.SchDoc


UHFKnifeReturn_S
StarboardKnifeReturn

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

http://www.apache.org/licenses/LICENSE-2.0

limitations under the License.
Mech_Interface_Starboard

C:\Users\nicho\AlbertaSat\projects\Hyperion Solar Panels\Starboard\Mech_Interface_Starboard.SchDoc


Starboard to Athena Burnwires/SPI

Starboard to Athena Magnetorquers

Starboard to Starboard Deployable

Starboard Deployable to EPS

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

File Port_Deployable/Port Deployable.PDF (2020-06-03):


(the "License"); you may not use or redistribute this file except in compliance with the License. You This file and the information within it are licensed under the terms of the Apache License, Version 2.0

may obtain a copy of the License at:
Unless required by applicable law or agreed to in writing, content distributed under the License is
distributed on an "AS IS" BASIS, WITHOUT WARRANTIES OR CONDITIONS OF ANY KIND, either express or implied. See the License for the specific language governing permissions and

http://www.apache.org/licenses/LICENSE-2.0

limitations under the License.
Port Deployable
Title

Letter
C:\Users\nicho\AlbertaSat\projects\Hyperion Solar Panels\Port Deployable\Port Deployable.SchDoc


1 2
1 7

9 | 1 3
2 1 | | 1 1

n within it are lic

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

http://www.apache.org/licenses/LICENSE-2.0

limitations under the License.
Current_Voltage_Sensor

C:\Users\nicho\AlbertaSat\projects\Hyperion Solar Panels\Common Schematics\Current_Voltage_Sensor.SchDoc


n within it are lic

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

http://www.apache.org/licenses/LICENSE-2.0

limitations under the License.
Temp_Sensor

C:\Users\nicho\AlbertaSat\projects\Hyperion Solar Panels\Common Schematics\Temp_Sensor.SchDoc

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

http://www.apache.org/licenses/LICENSE-2.0

limitations under the License.
XTJ-Prime_2S2P

C:\Users\nicho\AlbertaSat\projects\Hyperion Solar Panels\Common Schematics\XTJ-Prime_2S1P.SchDoc

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

http://www.apache.org/licenses/LICENSE-2.0

limitations under the License.
Mech_Interface_Port_Deployable

C:\Users\nicho\AlbertaSat\projects\Hyperion Solar Panels\Port Deployable\Mech_Interface_Port_Deployable.SchDoc

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

http://www.apache.org/licenses/LICENSE-2.0

limitations under the License.
Port_Deployable_Headers
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

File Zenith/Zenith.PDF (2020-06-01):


(the "License"); you may not use or redistribute this file except in compliance with the License. You This file and the information within it are licensed under the terms of the Apache License, Version 2.0

may obtain a copy of the License at:
Unless required by applicable law or agreed to in writing, content distributed under the License is
distributed on an "AS IS" BASIS, WITHOUT WARRANTIES OR CONDITIONS OF ANY KIND, either express or implied. See the License for the specific language governing permissions and

http://www.apache.org/licenses/LICENSE-2.0

limitations under the License.
Zenith
Title

Letter
C:\Users\nicho\AlbertaSat\projects\Hyperion Solar Panels\Zenith\Zenith.SchDoc


1 2
1 7

9 | 1 3
2 1 | | 1 1

n within it are lic

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

http://www.apache.org/licenses/LICENSE-2.0

limitations under the License.
Current_Voltage_Sensor

C:\Users\nicho\AlbertaSat\projects\Hyperion Solar Panels\Common Schematics\Current_Voltage_Sensor.SchDoc


n within it are lic

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

http://www.apache.org/licenses/LICENSE-2.0

limitations under the License.
Temp_Sensor

C:\Users\nicho\AlbertaSat\projects\Hyperion Solar Panels\Common Schematics\Temp_Sensor.SchDoc

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

http://www.apache.org/licenses/LICENSE-2.0

limitations under the License.
XTJ-Prime_2S2P

C:\Users\nicho\AlbertaSat\projects\Hyperion Solar Panels\Common Schematics\XTJ-Prime_2S1P.SchDoc

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

http://www.apache.org/licenses/LICENSE-2.0

limitations under the License.
Mech_Interface_Zenith

C:\Users\nicho\AlbertaSat\projects\Hyperion Solar Panels\Zenith\Mech_Interface_Zenith.SchDoc


Zenith to Athena Burnwires/SPI

Zenith to Athena Magnetorquers

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

http://www.apache.org/licenses/LICENSE-2.0

limitations under the License.
Zenith_Headers
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

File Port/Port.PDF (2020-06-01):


(the "License"); you may not use or redistribute this file except in compliance with the License. You This file and the information within it are licensed under the terms of the Apache License, Version 2.0

may obtain a copy of the License at:
Unless required by applicable law or agreed to in writing, content distributed under the License is
distributed on an "AS IS" BASIS, WITHOUT WARRANTIES OR CONDITIONS OF ANY KIND, either express or implied. See the License for the specific language governing permissions and

http://www.apache.org/licenses/LICENSE-2.0

limitations under the License.
Port
Title

Letter
C:\Users\nicho\AlbertaSat\projects\Hyperion Solar Panels\Port\Port.SchDoc


1 2
1 7

9 | 1 3
2 1 | | 1 1

n within it are lic

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

http://www.apache.org/licenses/LICENSE-2.0

limitations under the License.
Current_Voltage_Sensor

C:\Users\nicho\AlbertaSat\projects\Hyperion Solar Panels\Common Schematics\Current_Voltage_Sensor.SchDoc


n within it are lic

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

http://www.apache.org/licenses/LICENSE-2.0

limitations under the License.
Temp_Sensor

C:\Users\nicho\AlbertaSat\projects\Hyperion Solar Panels\Common Schematics\Temp_Sensor.SchDoc

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

http://www.apache.org/licenses/LICENSE-2.0

limitations under the License.
XTJ-Prime_2S2P

C:\Users\nicho\AlbertaSat\projects\Hyperion Solar Panels\Common Schematics\XTJ-Prime_2S1P.SchDoc


UHFKnifeReturn_S
StarboardKnifeReturn

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

http://www.apache.org/licenses/LICENSE-2.0

limitations under the License.
Mech_Interface_Port

C:\Users\nicho\AlbertaSat\projects\Hyperion Solar Panels\Port\Mech_Interface_Port.SchDoc


Port to Athena Burnwires/SPI

Port to Port Deployable

Port Deployable to EPS

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

http://www.apache.org/licenses/LICENSE-2.0
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

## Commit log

2020-05-21 Initial commit of Port project files.
    [Port Solar Panel.PcbDoc, Port.PrjPcb, Port.SchDoc]
2020-05-21 Initial commit of Port files.
    [Port Solar Panel.PcbDoc, Port.PrjPcb, Port.SchDoc]
2020-05-21 Initial commit of Port Deployable files.
    [Port Deployable Solar Panel.PcbDoc, Port Deployable.PrjPcb, Port Deployable.SchDoc]
2020-05-21 Initial commit for Starboard files.
    [Starboard Solar Panel.PcbDoc, Starboard.PrjPcb, Starboard.SchDoc]
2020-05-21 Initial commit for Starboard Deployable files.
    [Starboard Deployable Solar Panel.PcbDoc, Starboard Deployable.PrjPcb, Starboard Deployable.SchDoc]
2020-05-21 Initial commit for Zenith files.
    [Zenith.PrjPcb, Zenith.SchDoc]
2020-05-21 Adding ADC files.
    [AD7298 12-Bit SPI ADC.SchDoc]
2020-06-01 Added common schematic folder.
2020-06-03 Resized deployables.
    [Port Solar Panel.PcbDoc]
2020-06-28 SVN 2699
    [Mech_Interface_Port.SchDoc, Port Solar Panel.PcbDoc, Port.PrjPcb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]
2024-08-03 Reorganizing files and adding documentation.
    [20210528_Antenna_Saddle.step, 20210528_DFGM_Saddle.step, 20210528_Deployable_Switch_Depressor.step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]
2024-08-11 Reorganizing files again and adding 2U files.
    [Mech_Interface_Port.SchDoc, Mech_Interface_Port_Deployable.SchDoc, Mech_Interface_Starboard.SchDoc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]
